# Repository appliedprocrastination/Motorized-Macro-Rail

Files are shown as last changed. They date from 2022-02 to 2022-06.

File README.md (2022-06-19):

# OpenMacroRail Electronics Hardware
## Summary
PCB-design for controlling a motorized macro rail. Designed for photographers with electronics skills rather than engineers with photography skills. Main features:
- Zero surface mount components, and should therefore be possible to hand solder - even for people with novice soldering skills. 
- Flexible solution for connecting to most types of camera via 2.5mm stereo jack, pin header, or solder joints.
- Simple design for driving a single motor via a BTT TMC2209 V1.2 motor driver.
- Based on the WiFi-enabled NodeMCU 32S V2 DevKit. 
- Has broken out headers for connecting limit switches and rotary encoders (neither of which are used in the intended application the board was designed for).
- Total cost of around $30 (Camera, optics, motor, slider, and tools not included)

### Other parts of this project:
- [Firmware and web-interface](https://github.com/AppliedProcrastination/OpenMacroRail)
- [3D printable gears and PCB mount](https://www.printables.com/model/219042-motorized-camera-rail-for-macro-photography) 
- [3D printable microscope objective adapter](https://www.printables.com/model/218910-microscope-objective-adapter) (RMS Thread 160mm focal distance)
- [Canon EF/EF-S mount for the microscope adapter above](https://www.printables.com/model/218900-canon-efef-s-lens-mount-with-screw-holes)
- Section of README with links to other relevant documentation: [Various Documentation](#various-documentation)

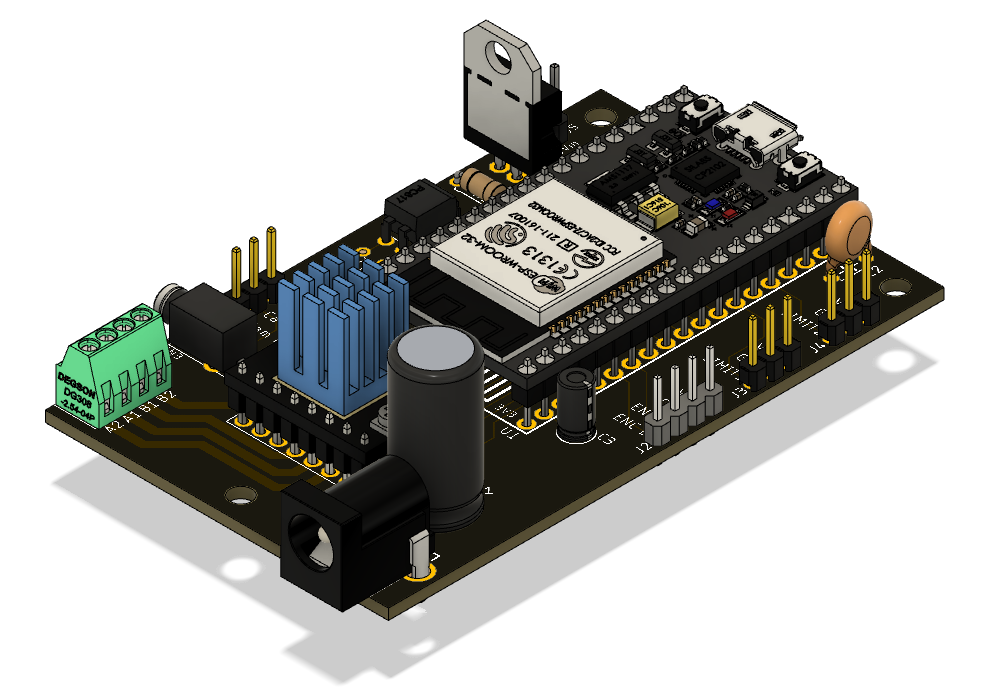
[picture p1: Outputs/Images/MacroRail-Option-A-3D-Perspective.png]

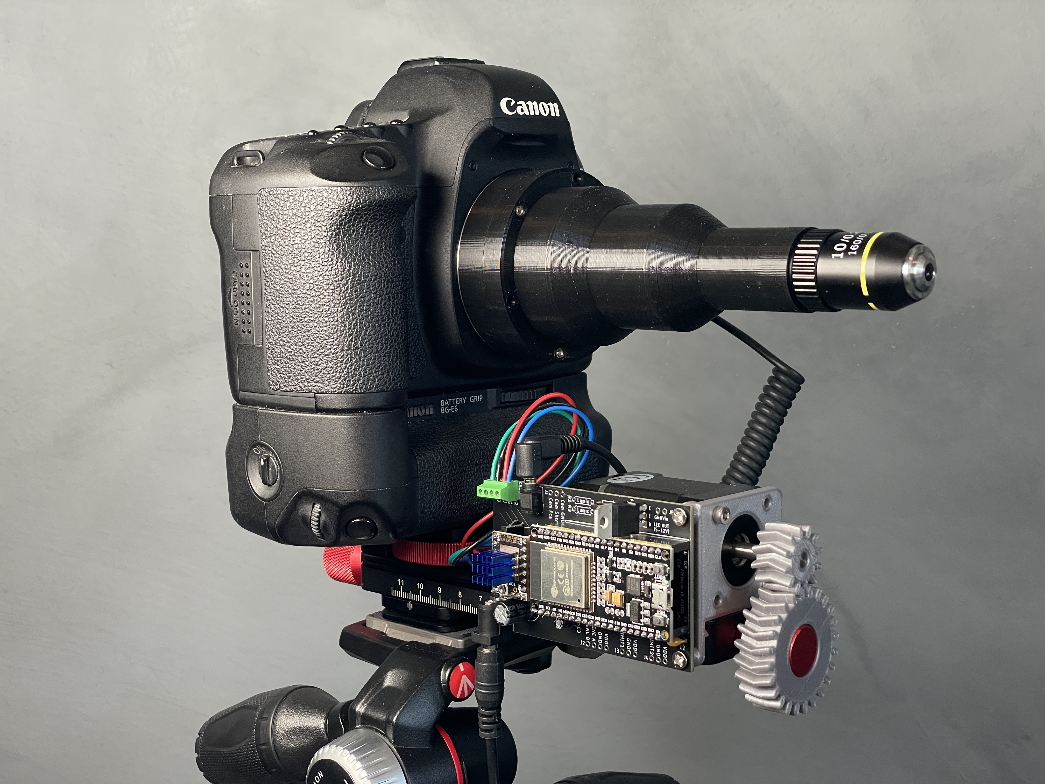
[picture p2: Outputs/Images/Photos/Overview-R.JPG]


## Configurability
The design is quite adaptable in general, and there are few components that are completely necessary for functioning (see the section "Minimum viable design"). There is however one part of the circuit that is particularly adaptable, and requires the users attention to guarantee a working configuration: the shutter control circuit - which depends on what kind of camera you are planning to control with this setup.

Snippet of schematic (DNP = Do Not Place):

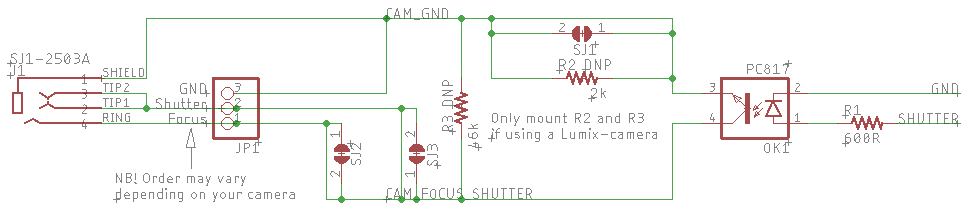
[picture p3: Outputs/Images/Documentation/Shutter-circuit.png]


As shown in the image above, there is a lot going on for what is normally a very simple circuit (you can trigger many cameras by simply short-circuiting all the pins in the remote shutter connector with a piece of wire). The reason for all this additional complexity is to keep the design as flexible as possible, and hopefully allow the PCB to be used with any type of camera. This is obviously not possible for me to test out in person, so I'm basing most of what follows on [this blog-post by Günter from LRTimelapse](https://lrtimelapse.com/news/intervalometer-hack/) (which is based on feedback from a solid photographer community) and private conversations with Stefan from [CNCKitchen](https://www.youtube.com/CNCKitchen) (as he owns a camera not mentioned in the above blog-post).

All the extra nick-nack is an attempt to solve the following design-requirements:
1. Different cameras require different signals to trigger
    - Example: 
        - Canon requires Shutter and GND to be shorted
        - Nikon/Sony requires Shutter, Focus and GND to be shorted
        - Lumix requires a [resistor network](https://i1.wp.com/fluxing.de/wp-content/uploads/2018/03/arduino-panasonic-lumix-shutter-schematic.jpg) between Shutter and GND.
2. Different cameras may swap the layout of Shutter and Focus signals on the 2.5mm jack
3. The user may not own a connector with a 2.5mm jack, so a pin header/2.54mm pitch solder joint option is also provided.
4. The high currents drawn by the motor may cause noise on the PCB, so therefore the shutter circuit is optically isolated from the rest of the electronics to avoid unintended triggering of the camera shutter.

The following components are layed out in the design solely to handle requirements 1. and 2.
- SJ1, SJ2, SJ3
- R2, R3 (Note: These are, to my knowledge, only required by Lumix - and should not be mounted by default)

The solder jumpers (SJ1-3) are there to give the user an opportunity to make permanent (but recoverable) changes to the circuit. The way this works is that each SJ consists of two exposed copper pads with a small trace connecting the pads. Cutting the trace with a scalpel will remove the connection between the pads, but it is still possible to recover this connection by applying a bit of solder as a bridge between the pads (in case the user buys a new camera, or just cut the wrong wire).

### An example of how to use solder jumpers:
Suppose your camera starts updating the screen each time the autofocus-signal is activated (even in manual focus mode), so you want to stop that signal from being activated each time a picture is captured. In this scenario, you can use a scalpel to break the wire connecting the two pads of SJ2 by cutting along the red arrow in the following picture: 

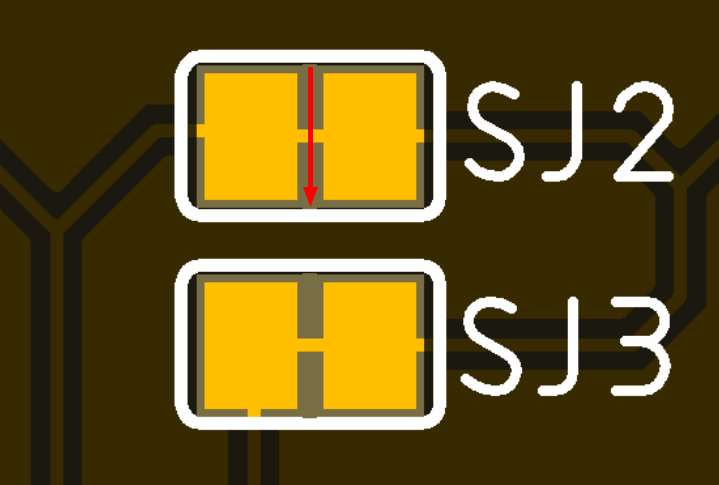
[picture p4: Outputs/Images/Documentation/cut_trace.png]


### Default configuration (Canon,Nikon,Sony):
The default configuration requires you to not mount R2 and R3. The pads on all the solder jumpers are shorted by default, meaning that a simplified schematic of the circuit looks like this:

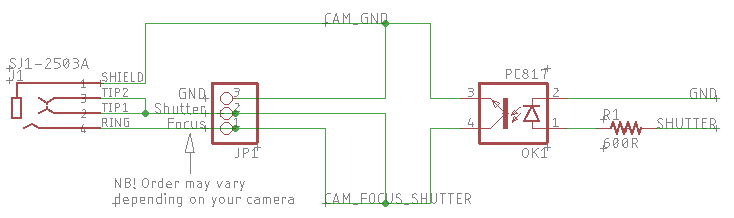
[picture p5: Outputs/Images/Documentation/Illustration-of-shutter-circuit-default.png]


This should work for most Canon, Nikon, and Sony cameras.

### Lumix configuration:
To use the shutter circuit with a Lumix camera, the resistor network must be mounted (R2 and R3). Keep in mind that SJ1 is shorted by default, meaning that it needs to be cut in order for R2 to take any effect.

Mount R2 and R3, then use a scalpel to break the wire in SJ1 by cutting along the red arrow in this picture.

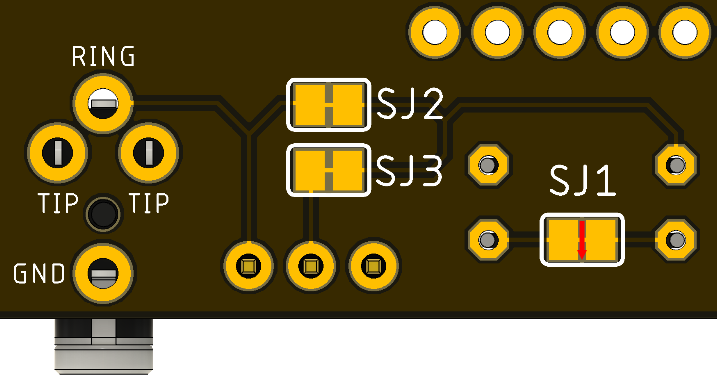
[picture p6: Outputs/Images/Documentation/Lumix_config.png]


Cutting this wire will activate R2 and leave you with the following schematic:

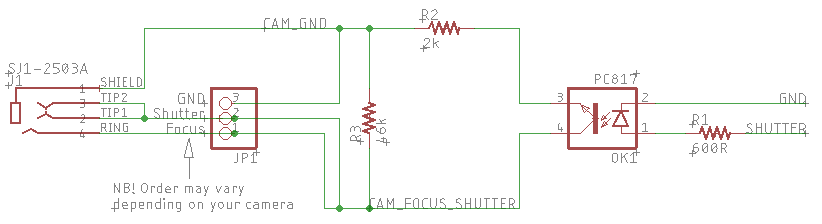
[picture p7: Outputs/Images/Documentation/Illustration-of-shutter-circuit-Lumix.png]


## Layout Options 
In the folder named Outputs/Gerber you will find design files that can be sent to a PCB manufacturer for production. There are two options, A and B, which differ only in the orientation of the power connector. 
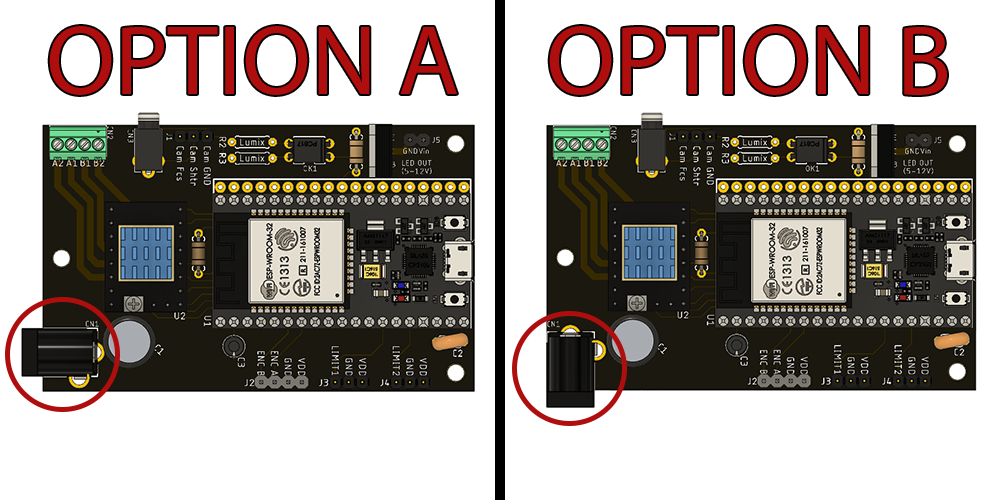
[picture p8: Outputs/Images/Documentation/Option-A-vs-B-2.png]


The reason that there are two options is to accommodate for mounting the PCB on different tripod designs. Keep in mind that the PCB is mounted on a moving part of the macro rail, so protruding parts may get stuck or bent by the force from the motor.
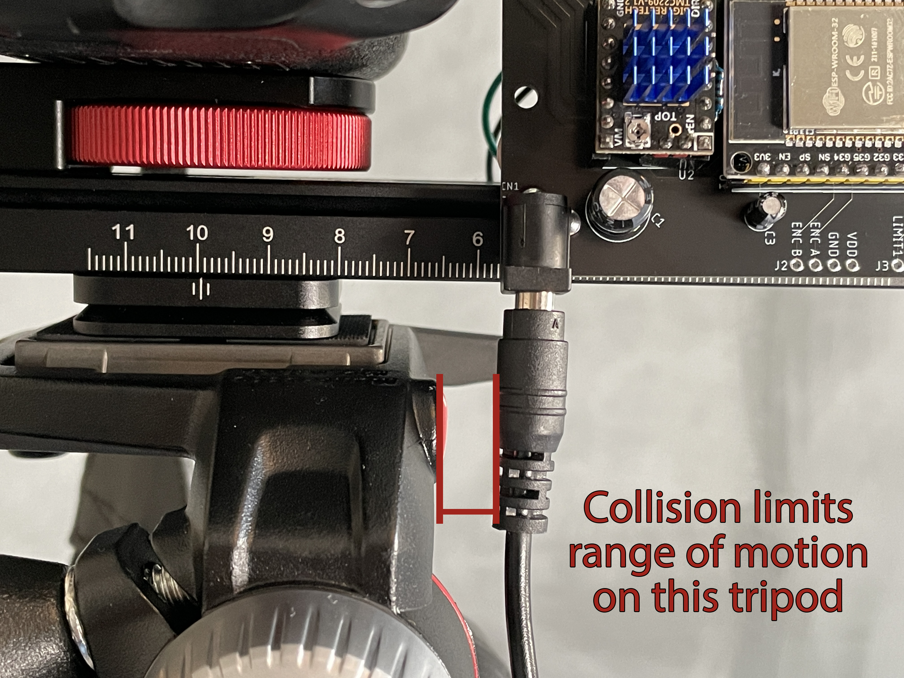
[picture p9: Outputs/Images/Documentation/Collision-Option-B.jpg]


## Bill Of Materials (BOM)
*Most of the AliExpress links are affiliate links. Prices are estimates and may vary with your location (shipping cost)*

### On PCB:
 - [PCB itself](./Outputs/Gerber/MacroRail_V1_0-2022-02-26.zip). Ca $10 at JLCPCB
 - 1x [TMC2209-V1.2](https://s.click.aliexpress.com/e/_9uc1XB) Stepper motor driver ([Documentation](https://github.com/bigtreetech/BIGTREETECH-TMC2209-V1.2/)). ca $8
 - 1x [NodeMCU 32s V2](https://www.aliexpress.com/item/1005001636295529.html) Dev kit (38-pin version) ([Documentation](https://docs.ai-thinker.com/en/esp32/boards/nodemcu_32s)) ca $5
 - 1x [PC817 Optocoupler](https://s.click.aliexpress.com/e/_AAgoAp) ca $1
 - 1x [100 uF capacitor (35V)](https://s.click.aliexpress.com/e/_ADnqKh) ca $1
 - 1x [10 uF capacitor (25V)](https://s.click.aliexpress.com/e/_ADnqKh) ca $1
 - 1x [1 uF capacitor](https://s.click.aliexpress.com/e/_9j2jOz) ca $1
 - 1x [2.1 mm Barrel Jack (power)](https://s.click.aliexpress.com/e/_Aq01NT) ca $1
 - 1x [Selection of resistors](https://s.click.aliexpress.com/e/_AOqGqt) (depending on your camera) ca $1
    - Note: R1 and R4 must always be mounted (these are 600 Ohm and 1k Ohm resistors respectively)
 - 1x [SJ1-2503A 2.5 mm stereo jack receptacle (for shutter cable)](https://no.mouser.com/ProductDetail/CUI-Devices/SJ1-2503A?qs=WyjlAZoYn52728cbIH3aBA%3D%3D) ca $1 (optional)
 - 1x [4-pin screw terminal block](https://s.click.aliexpress.com/e/_97dipR) ca $2 (optional)
 - 1x [TIP120 transistor (for powering external LED lighting)](https://s.click.aliexpress.com/e/_ApnAYv) ca $1 (optional) 
 - 3x [3-pin pin row](https://s.click.aliexpress.com/e/_ABvcat) ca $1 (optional)
 - 1x [4-pin pin row](https://s.click.aliexpress.com/e/_ABvcat) ca $1 (optional)
 - 1x [2-pin pin row](https://s.click.aliexpress.com/e/_ABvcat) ca $1 (optional)
 - 2x [19-pin pin header](https://s.click.aliexpress.com/e/_AFHrY5) ca $2 (optional)
 - 2x [8-pin pin header](https://s.click.aliexpress.com/e/_AFHrY5) ca $1 (optional)
 - 1x [2-pin pin header](https://s.click.aliexpress.com/e/_AFHrY5) ca $1 (optional)

 Total on PCB: ca $40 ($29 when excluding optional components)

### Outside of PCB:
Mandatory parts:
 - [Macro Rail](https://s.click.aliexpress.com/e/_9IiOvB) ca. $20 
 - [Nema 14 high torque motor](https://s.click.aliexpress.com/e/_ArX3ot) (High torque may be unnecessary for moving compact cameras) ca $20
 - RMS threaded microscope lens (focused to 160mm). [Example](https://s.click.aliexpress.com/e/_9zATGv) ca $8
 - 5-12V Power supply (current can be limited with TMC2209 if 5V is too much for your motor). [Example](https://s.click.aliexpress.com/e/_AC81D7) ca $8 
 - Cable for shutter release that fits your camera (you can either use the 2.5mm jack receptacle or cut the cable and solder it directly to the PCB via JP1)
    - [Example for various cameras](https://s.click.aliexpress.com/e/_9iNl7J) ca $3

Parts that can be 3D-printed if you design something that suits your camera:
 - Bellow spacer that fits your camera (with converters to hold the microscope lens). This is optional, and can be 3D printed instead. 
    - Examples for Canon 5D:
        - [Bellow spacer](https://s.click.aliexpress.com/e/_A5xnYt) ca $40
        - [EFS to M24 converter](https://s.click.aliexpress.com/e/_9QvErF) ca $5
        - [M42 to RMS converter](https://s.click.aliexpress.com/e/_9QPTOd) ca $5
 
Total outside of PCB: ca $109 ($59 when excluding parts that can be 3D-printed)

## Preview

### Top

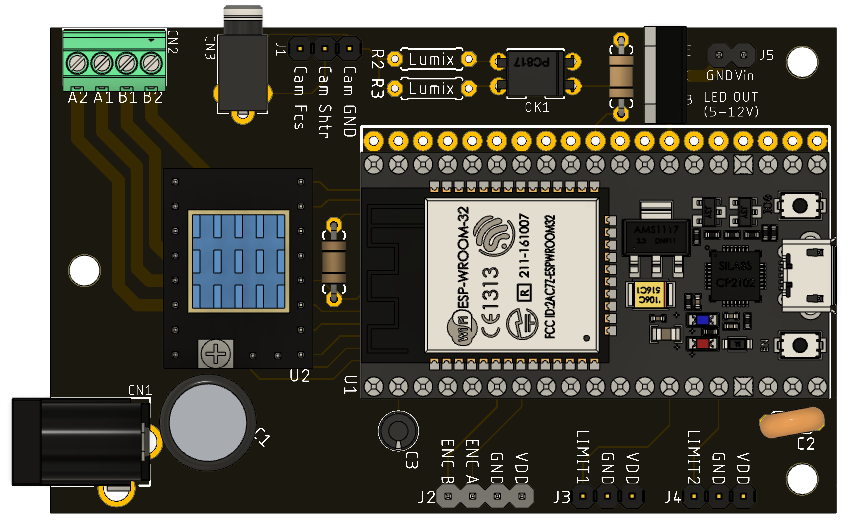
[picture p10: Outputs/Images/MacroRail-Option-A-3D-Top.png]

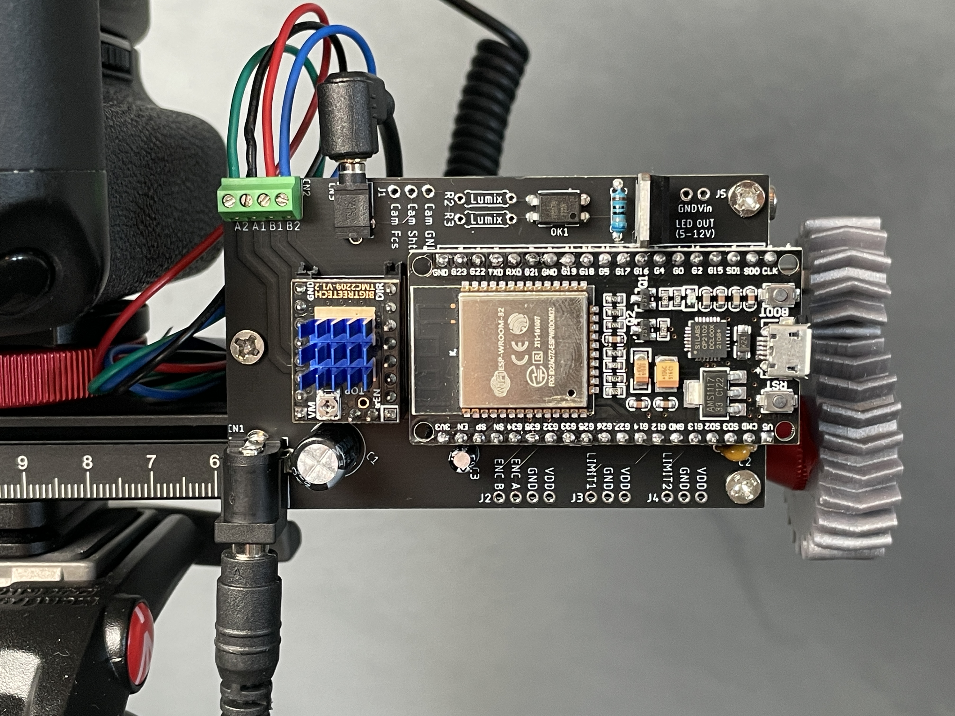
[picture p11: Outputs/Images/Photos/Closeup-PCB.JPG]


### Bottom

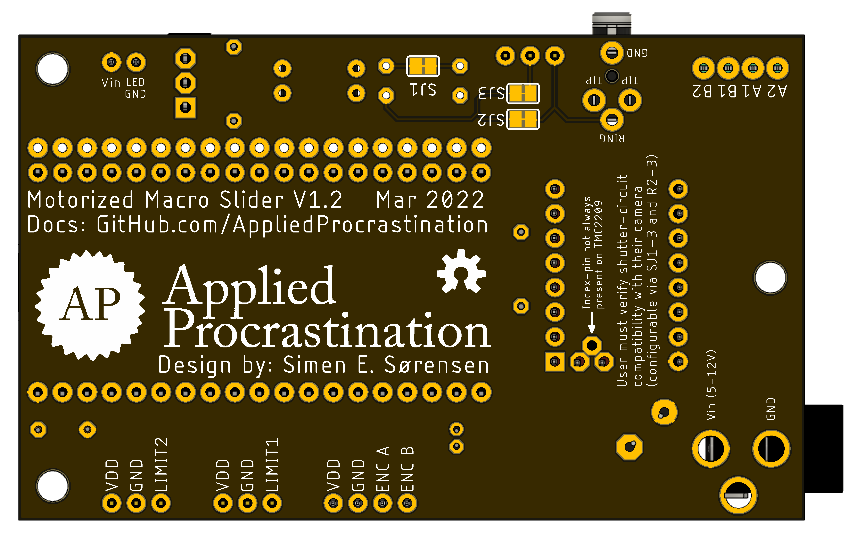
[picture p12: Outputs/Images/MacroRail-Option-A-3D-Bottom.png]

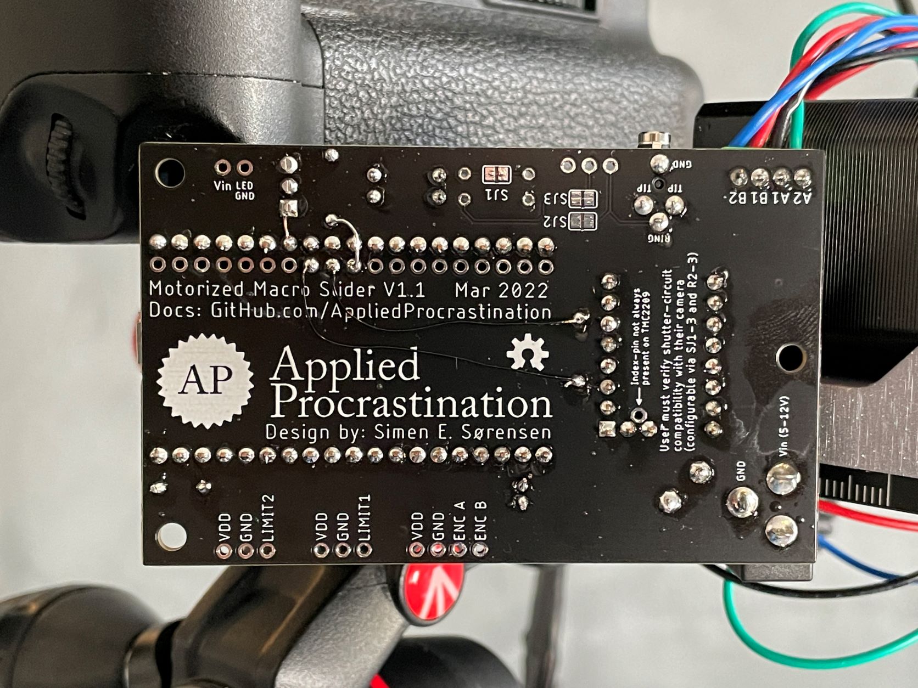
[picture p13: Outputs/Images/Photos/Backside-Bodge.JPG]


### Minimum viable design
Note: You may need to mount more resistors to get a minimum viable design (depending on your camera)

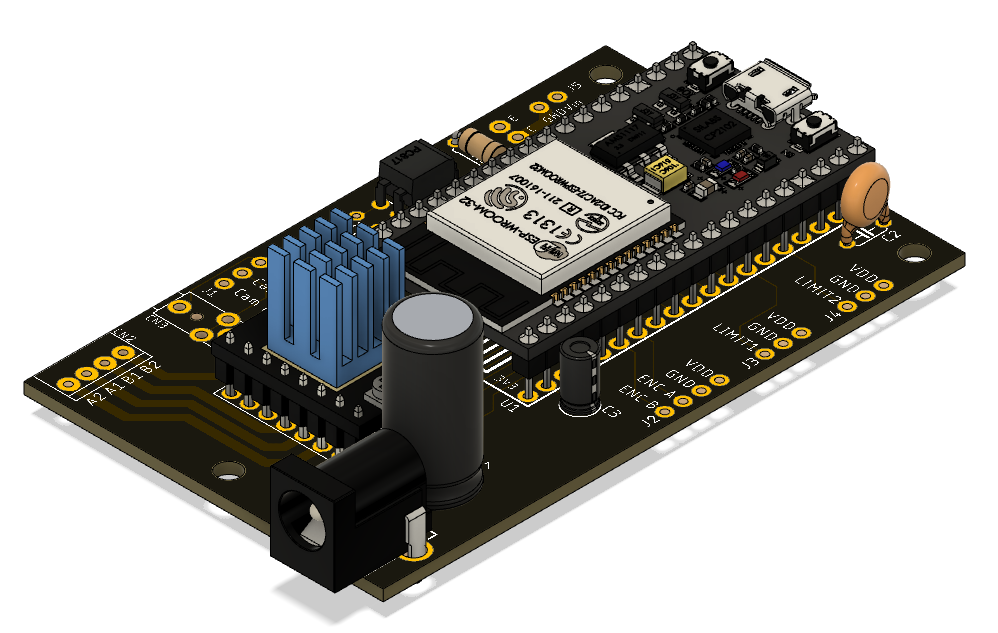
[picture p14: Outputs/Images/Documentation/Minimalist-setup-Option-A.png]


## How to order a printed circuit board (PCB)?
If you are interested in this project, and feel comfortable soldering electronic components, but have never ordered a custom PCB before this section is for you. 

Hobby-grade PCB manufacturers have made the process of ordering custom PCBs incredibly simple (and cheap) over the last few years, so for a low complexity board like this one, ordering can be done without any prior knowledge of the manufacturing process. 

### Step by step guide:

1. Decide whether you want your power connector oriented sideways (Option A) or downwards (Option B). Try to think about whether the power cable may get in the way of movement the tripod you plan to mount your macro rail to. See the section about [Layout Options](#layout-options) for more info.
2. Download the .zip file corresponding to your preferred layout option from the folder [/Outputs/Gerber](/Outputs/Gerber/). This is the design file that you will send to the manufacturer for fabrication.
3. Go to your preferred PCB manufacturers website and upload the gerber file. This board was designed for using https://www.jlcpcb.com, which is a very cheap, and fast, hobby-grade manufacturer. 

4. Once the upload is complete, you will see a preview of the board, and the web-tool will have learned most of the important parameters of the design (like the size, how many layers of copper it contains, etc.)
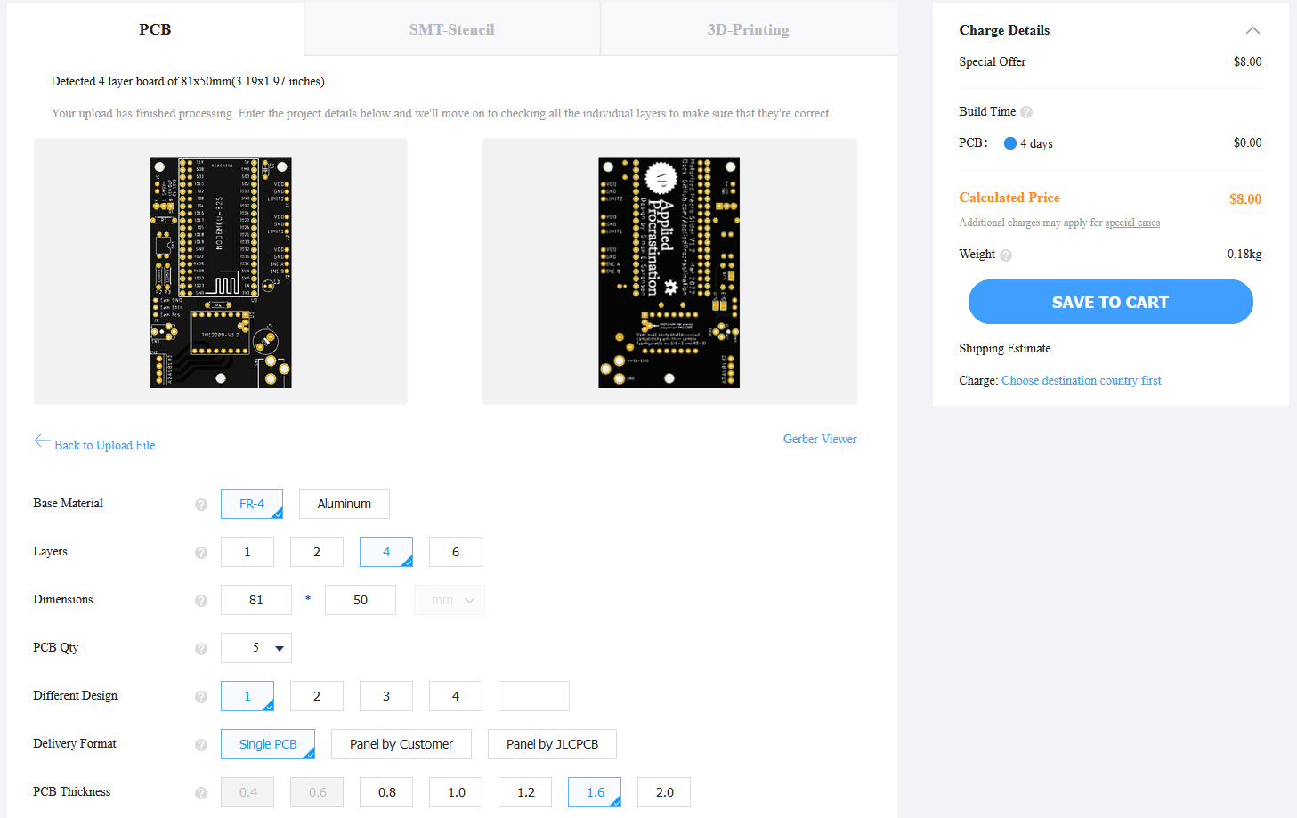
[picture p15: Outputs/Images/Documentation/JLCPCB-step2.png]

5. There's only one important thing you may need to fill in, which is the order of the layers. For some reason, the web-tool doesn't recognize the _l1, _l2, _l3, and _l4, suffixes of each layer, so you need to select these layers as shown in the image below. 
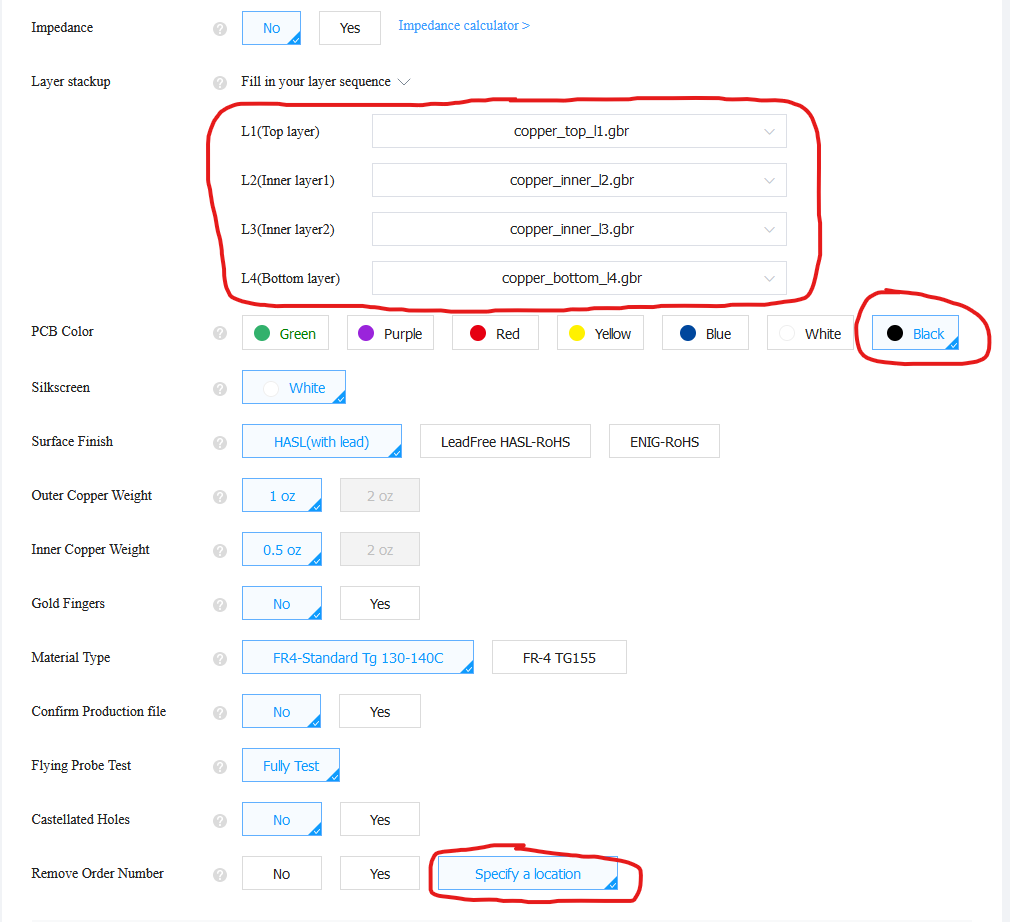
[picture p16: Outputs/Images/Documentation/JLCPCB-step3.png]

While you are at it, make sure to select the sexy black soldermask, and click "specify a location" for the order number. The last setting will ensure that the manufacturer doesn't place an order number anywhere important, but rather replace a predefined string like shown here:
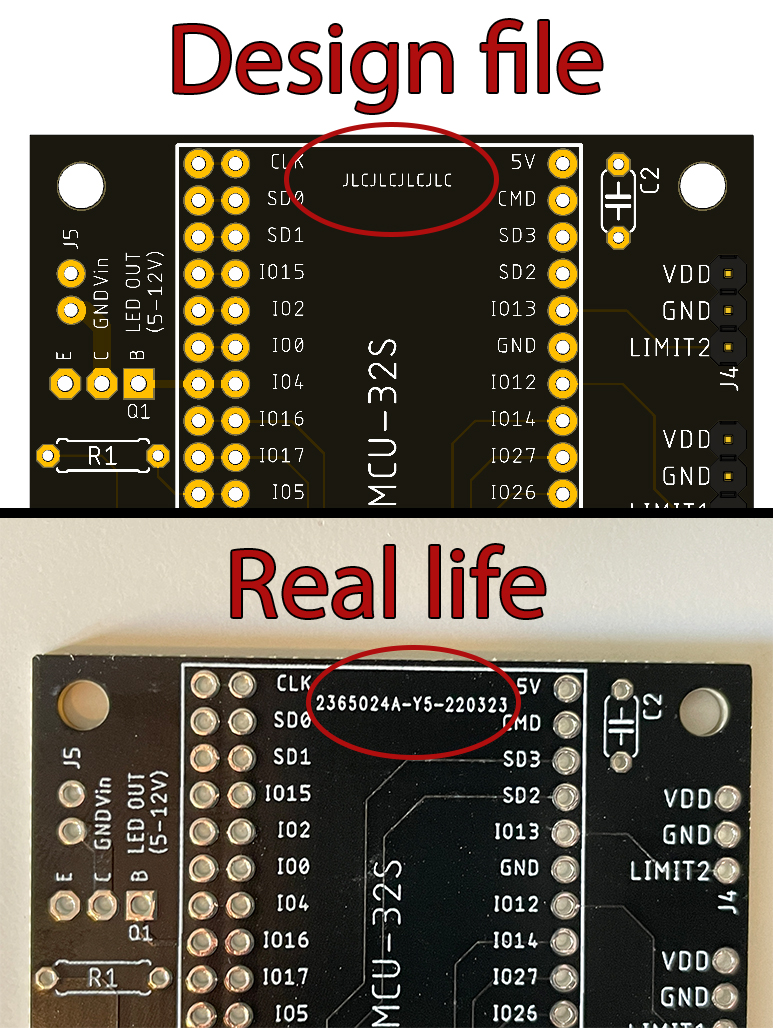
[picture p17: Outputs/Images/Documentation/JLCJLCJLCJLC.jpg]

6. That's it! Click "Save to cart", pay, and the board will be manufactured and shipped towards you within a two or three days (typically). Note that there is a cheap shipping option kind of hidden in the menu. If you didn't already have all the other necessary components in your electronics stockpile, it might be a good idea to consider this "slow" shipping option since you are already waiting for other stuff. In my experience, the PCBs arrive between 2 and 3 weeks after placing your order (when using the cheapest shipping option).
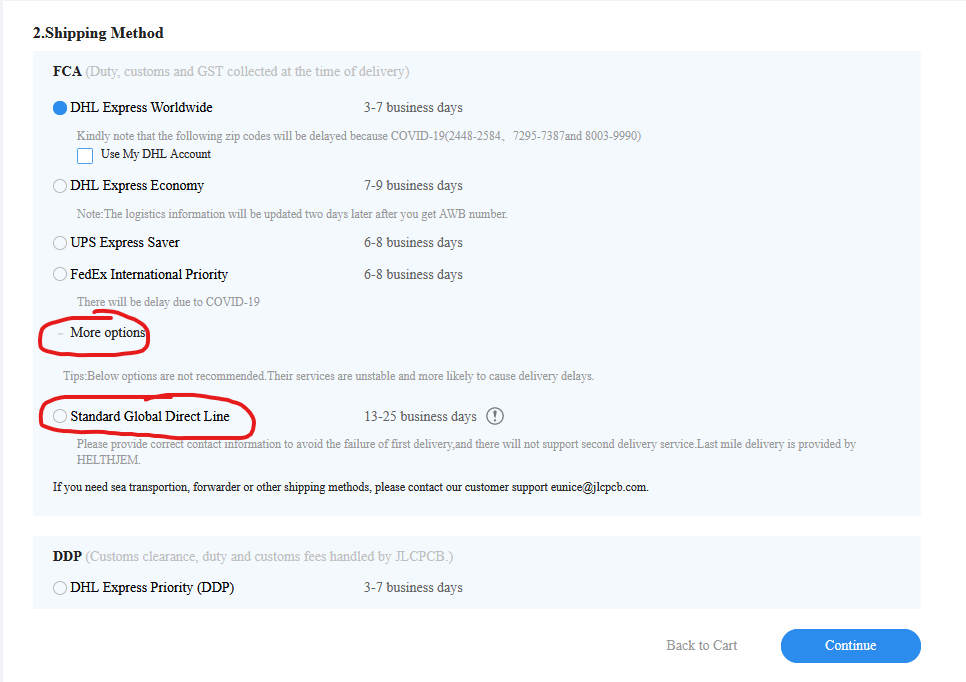
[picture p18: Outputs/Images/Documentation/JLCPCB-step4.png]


## Various documentation:
- [NodeMCU-32S Core Development Board](https://docs.ai-thinker.com/en/esp32/boards/nodemcu_32s)
- [NodeMCU Arduino Core (Software)](https://github.com/espressif/arduino-esp32)
- [TMC2209-V1.2 manual (Motor driver module)](https://github.com/bigtreetech/BIGTREETECH-TMC2209-V1.2/blob/master/manual/TMC2209-V1.2-manual.pdf)
- [TMC2209 datasheet (chip itself)](https://www.trinamic.com/fileadmin/assets/Products/ICs_Documents/TMC2209_datasheet_rev1.07.pdf)

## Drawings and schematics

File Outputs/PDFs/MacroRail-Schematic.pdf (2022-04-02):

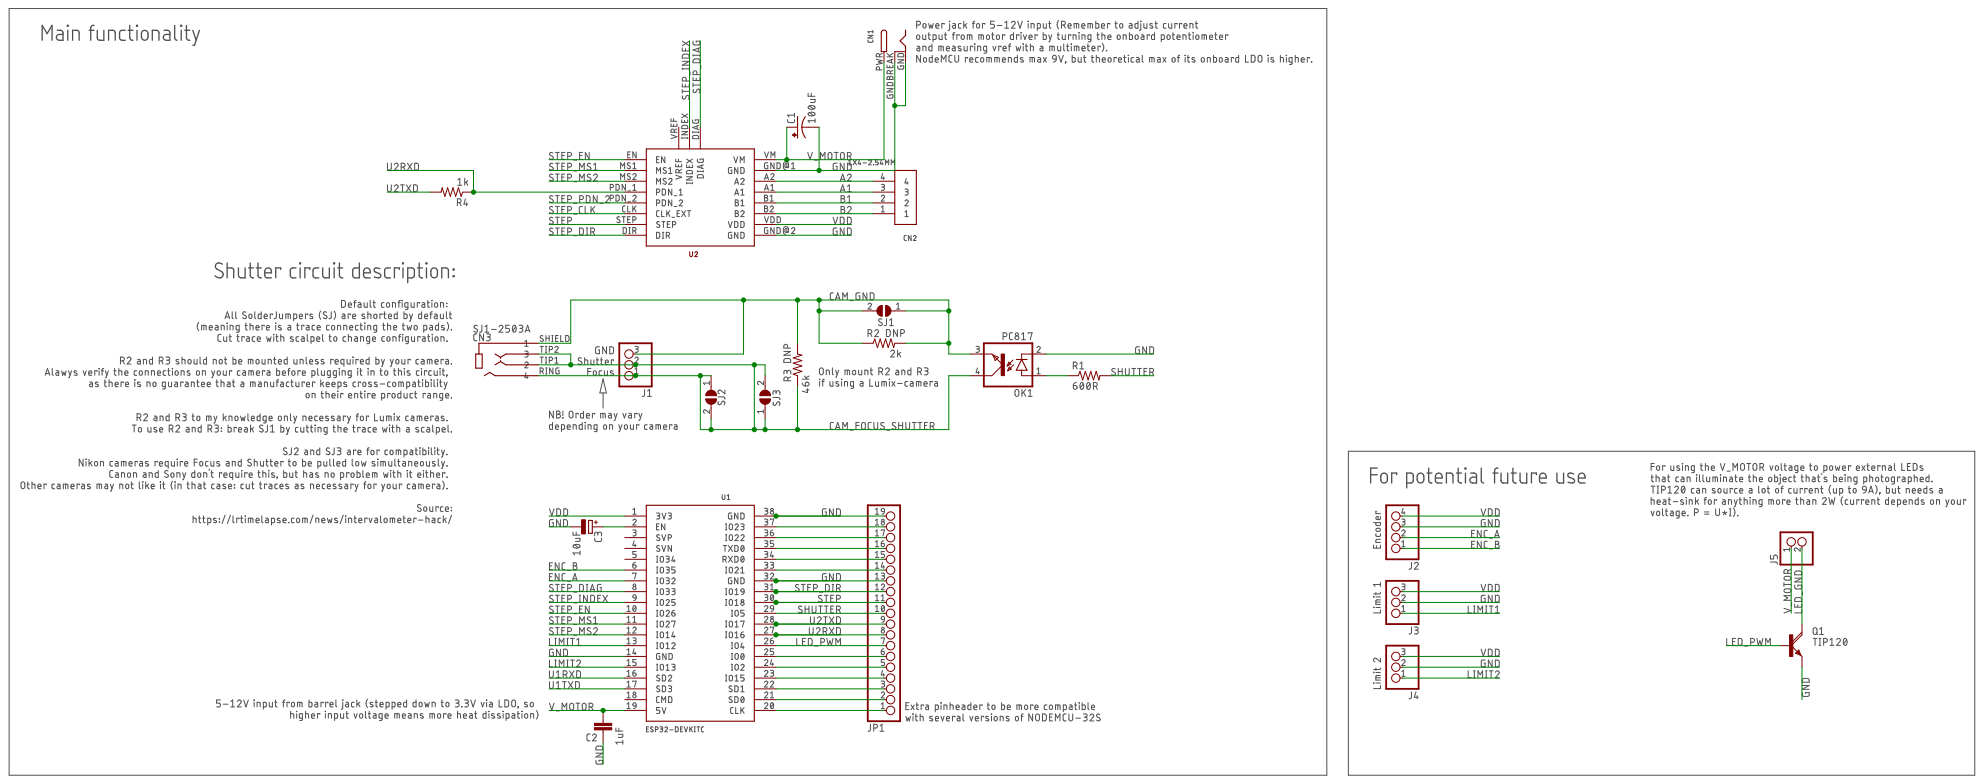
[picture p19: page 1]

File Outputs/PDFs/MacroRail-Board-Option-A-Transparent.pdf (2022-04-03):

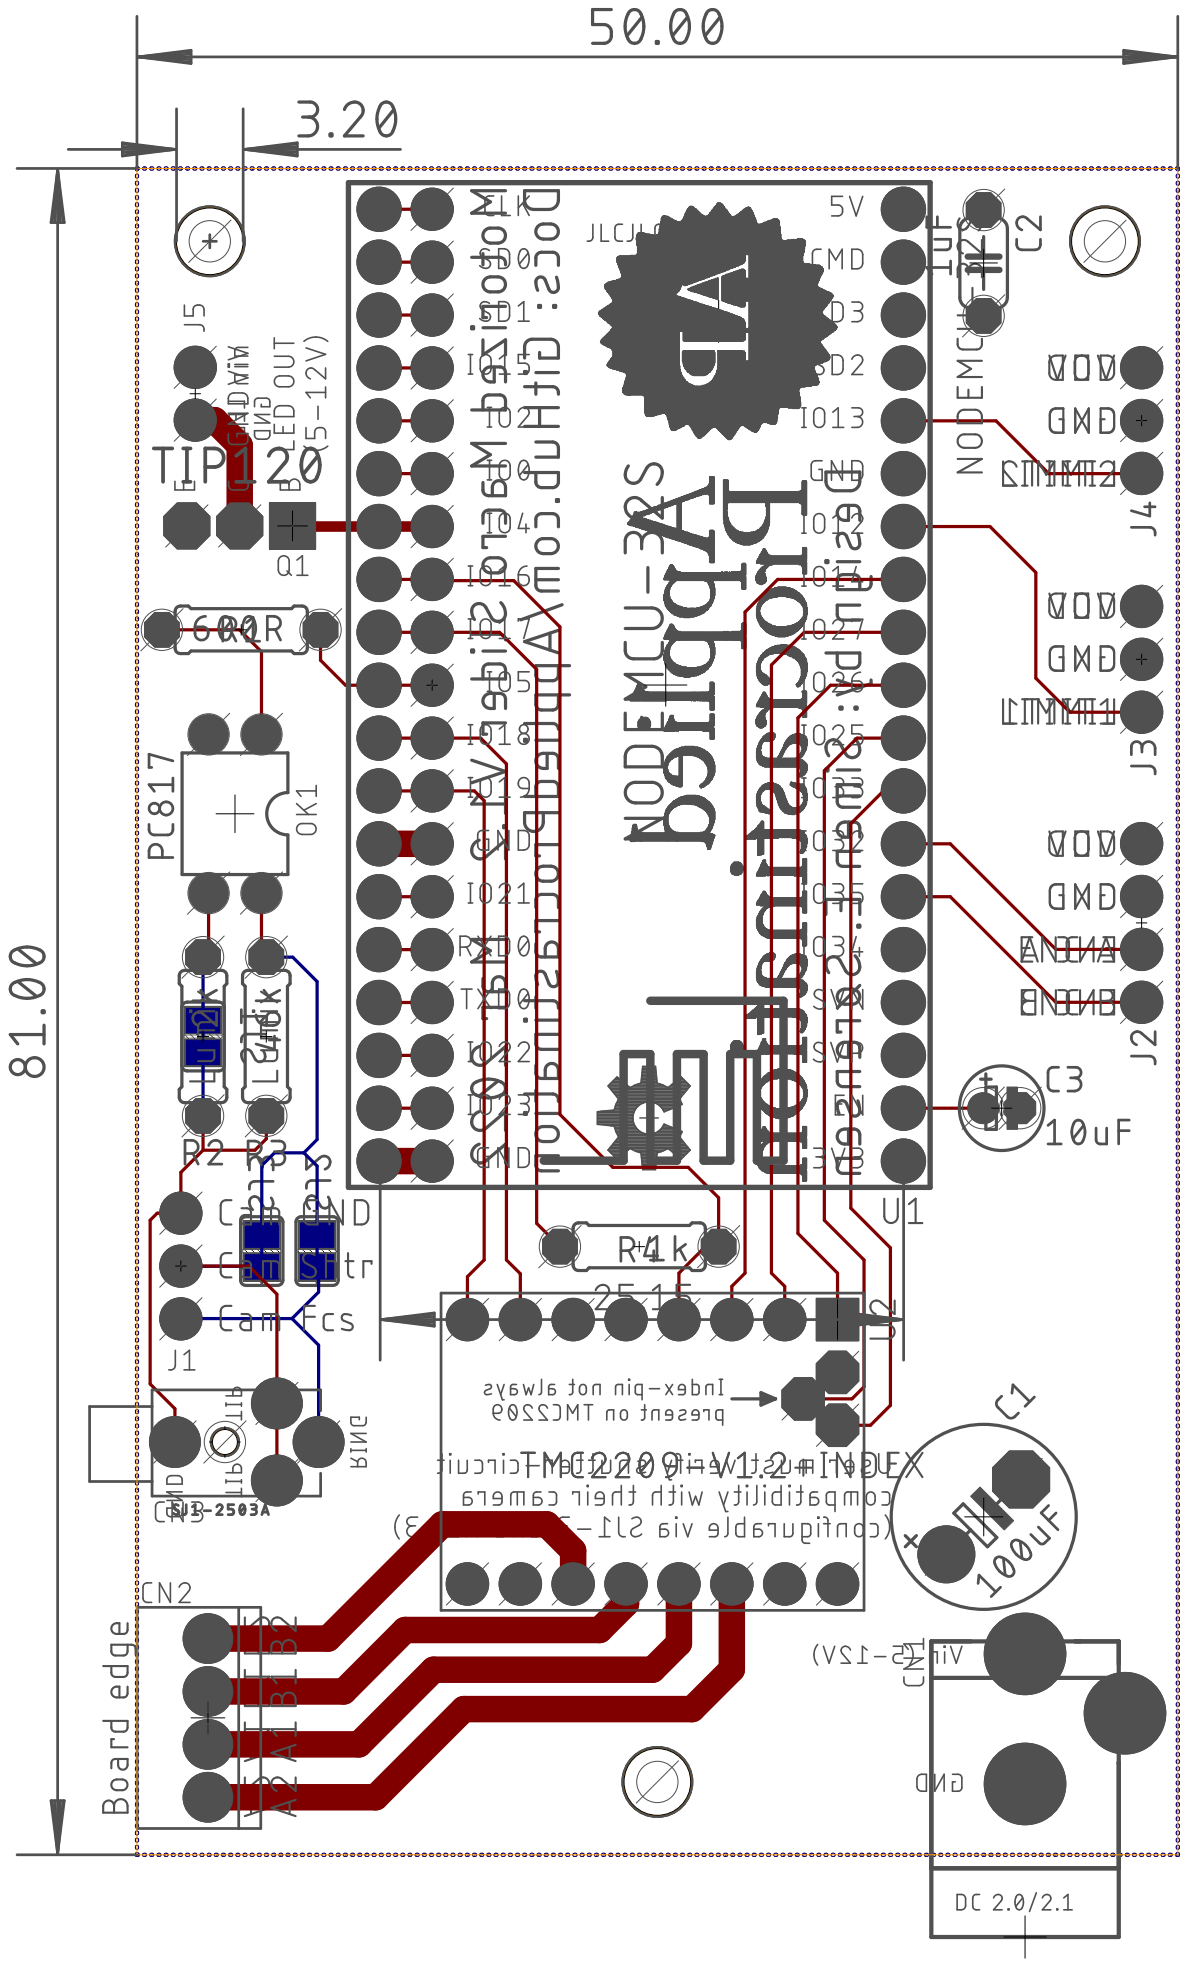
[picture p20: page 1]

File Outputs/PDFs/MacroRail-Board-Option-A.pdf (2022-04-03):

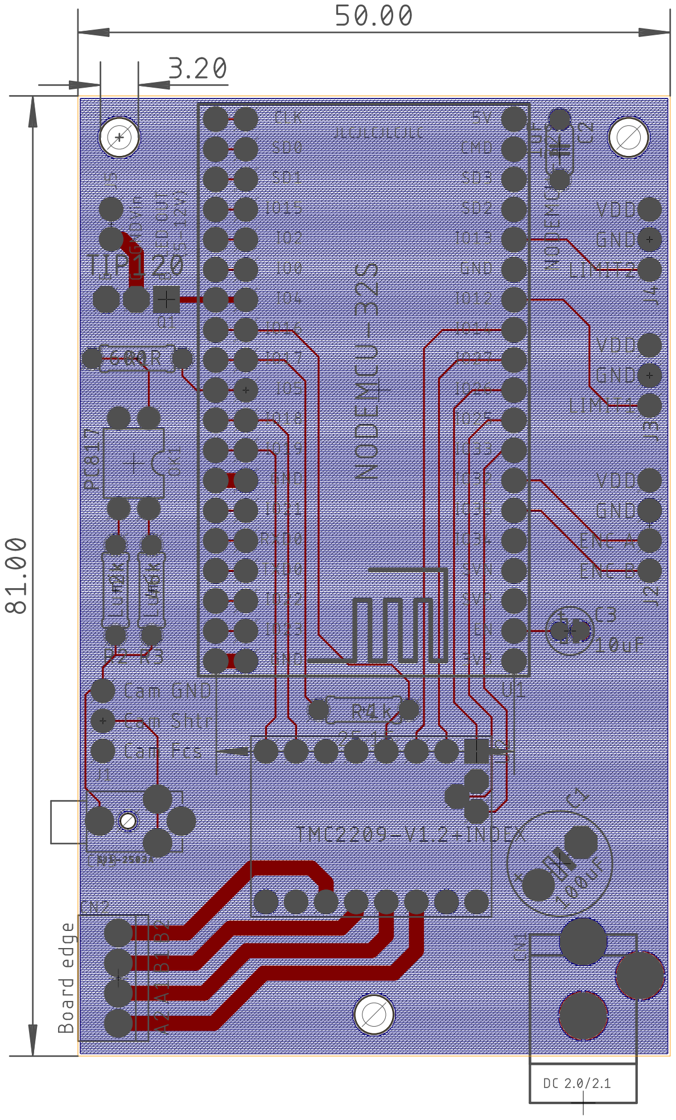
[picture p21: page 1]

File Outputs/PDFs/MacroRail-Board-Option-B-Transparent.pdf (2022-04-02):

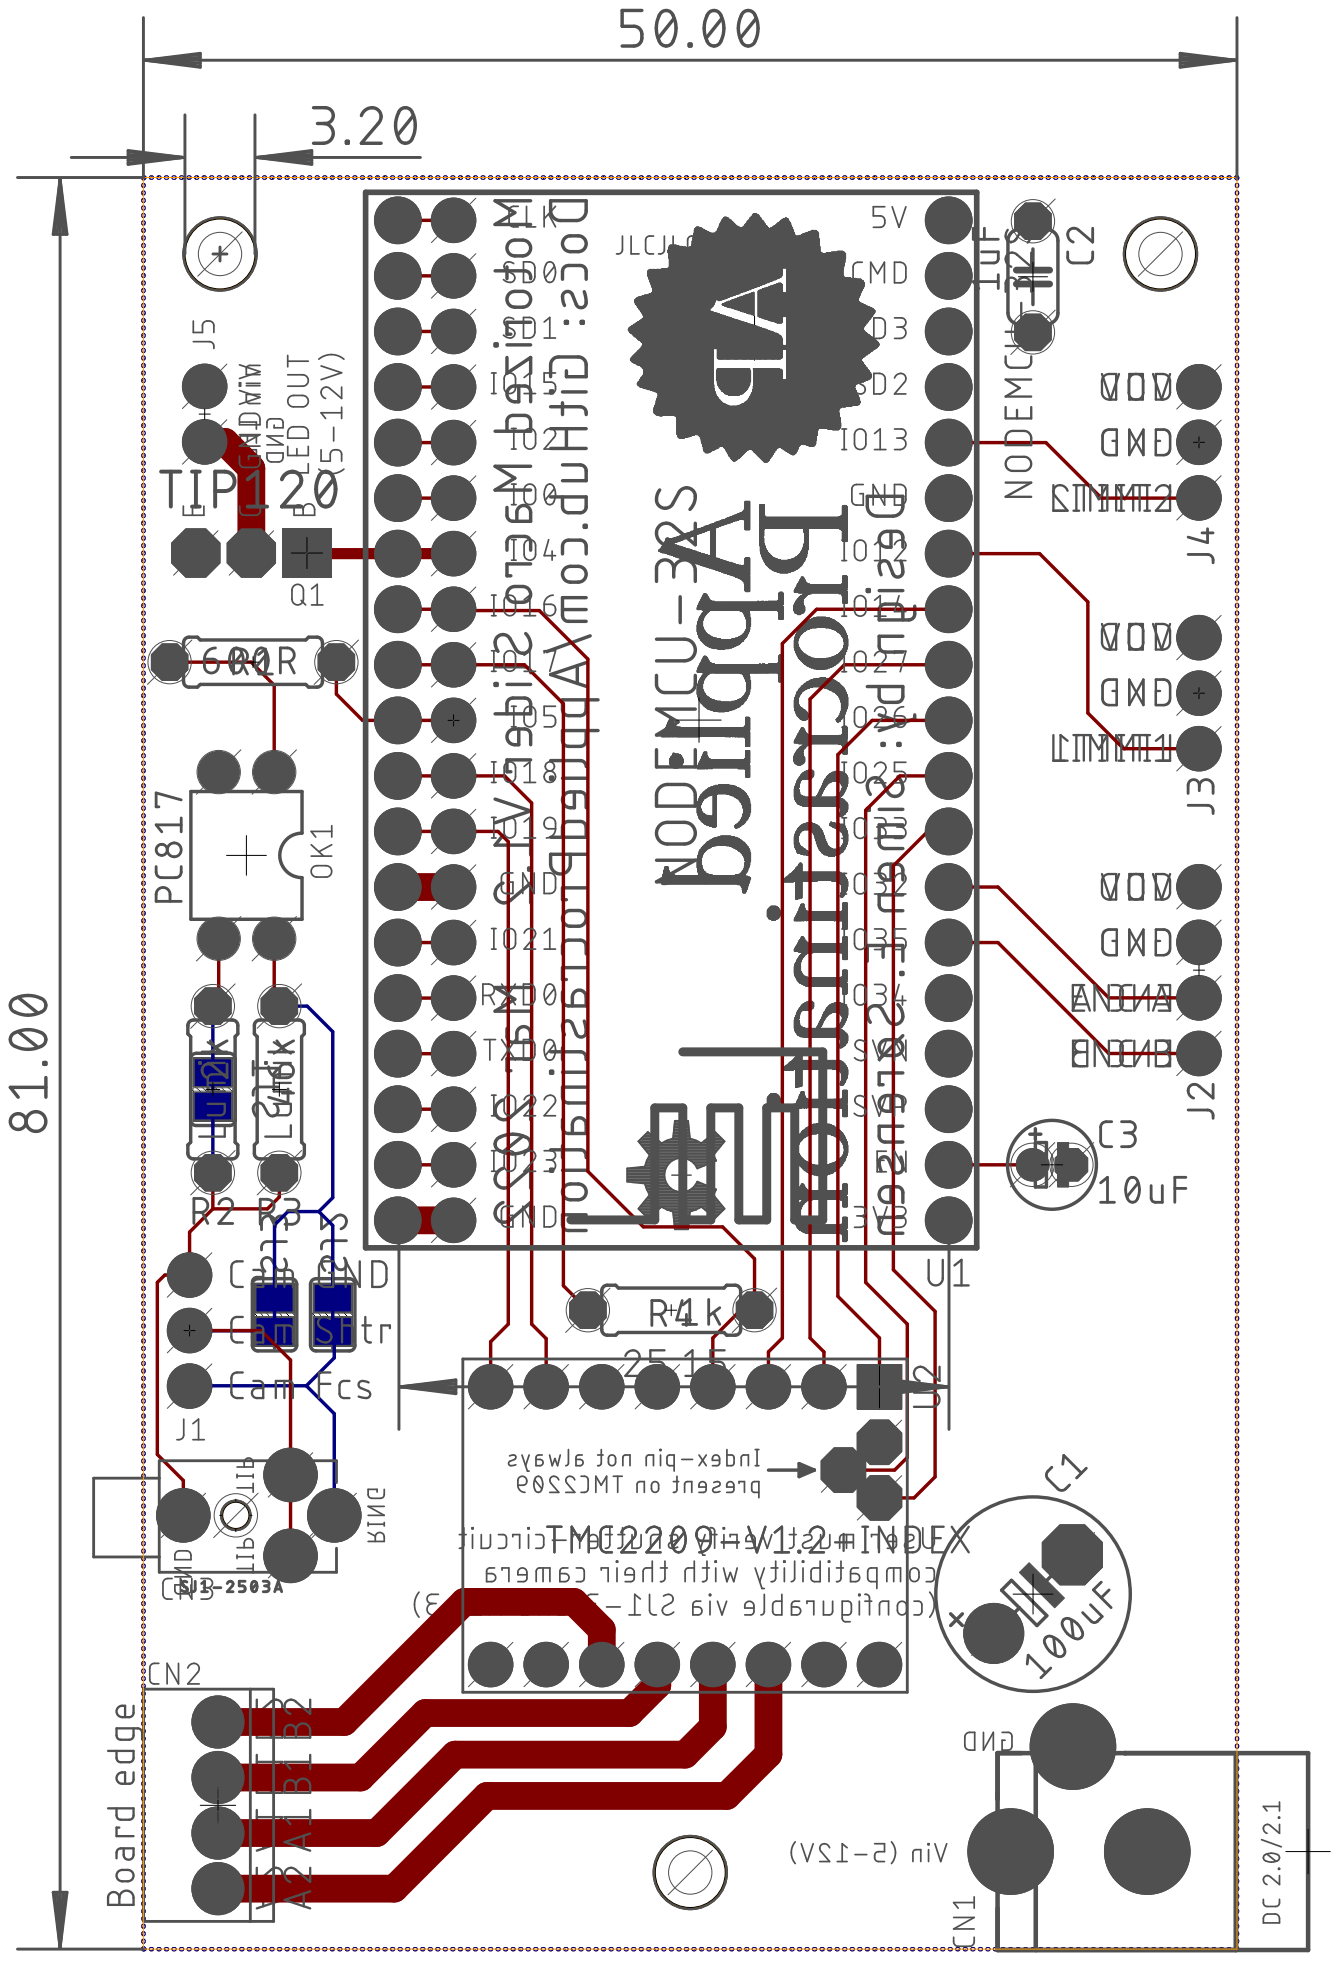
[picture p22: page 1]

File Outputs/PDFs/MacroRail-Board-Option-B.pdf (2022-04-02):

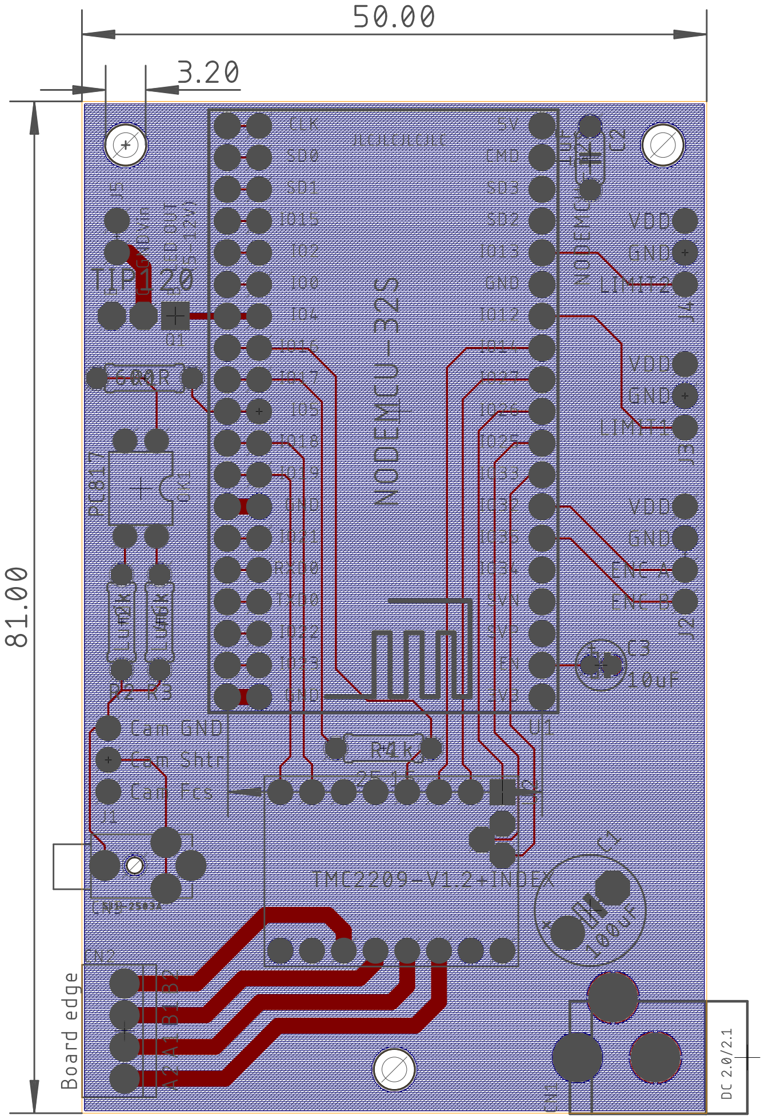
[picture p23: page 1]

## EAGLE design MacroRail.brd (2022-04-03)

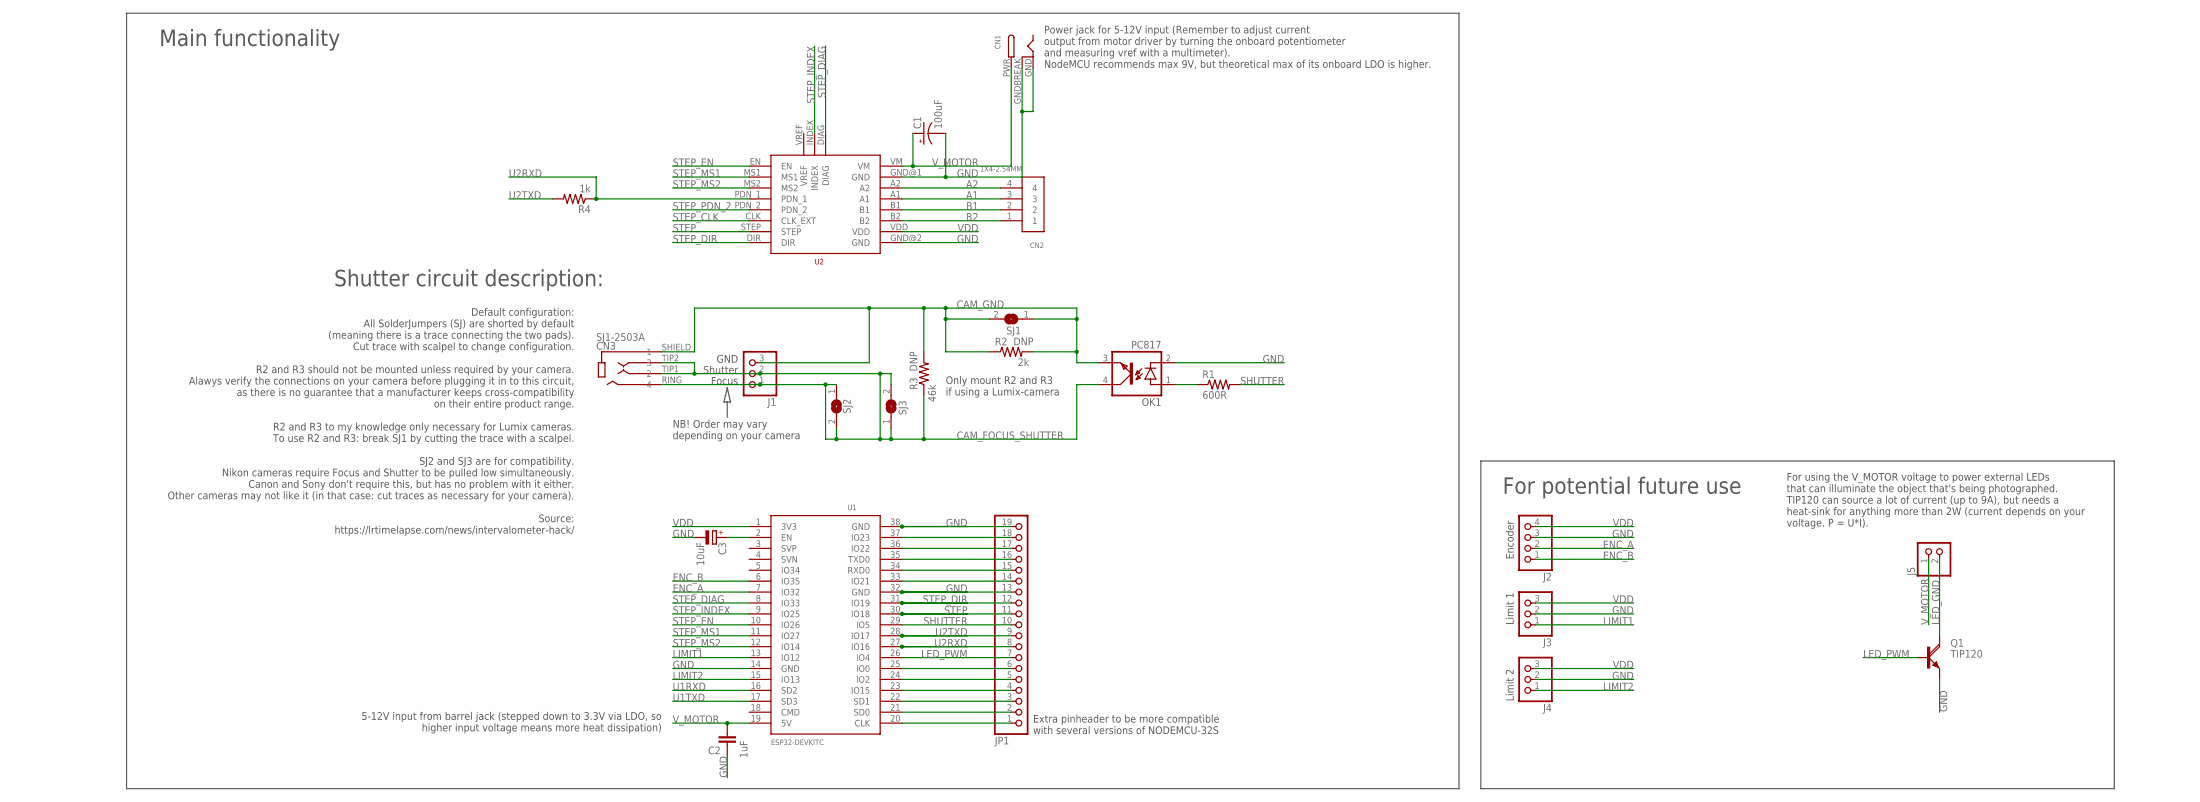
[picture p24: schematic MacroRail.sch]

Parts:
C1: 100uF; E5-8,5
C2: 1uF; C050-024X044
C3: 10uF; E1,8-4
CN1: DCBARRELPTH; DCJACK_2MM_PTH
CN2: 1X4-2.54MM; 1X04-2.54MM
CN3: SJ1-2503A; STEREOJACK2.5MM_STEREOJACK2.5MM
J1, J3, J4: PINHD-1X3CB; 1X03-CLEANBIG
J2: PINHD-1X4; 1X04
J5: PINHD-1X2CLEAN; 1X02CLEAN
JP1: PINHD-1X19; 1X19
OK1: PC817; DIL04
Q1: TIP120; TO220AH
R1: 600R; 0207/7
R2: 2k; 0207/7
R3: 46k; 0207/7
R4: 1k; 0207/7
SJ1, SJ2, SJ3: SJ
U1: ESP32DEVKITCWIDE; NODEMCU-32S
U2: TMC2209-V1.2+INDEX; BIGTREETECH-TMC2209-V1.2+INDEX

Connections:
A1: CN2.3, U2.A1
A2: CN2.4, U2.A2
B1: CN2.2, U2.B1
B2: CN2.1, U2.B2
CAM_FOCUS_SHUTTER: CN3.RING (4), CN3.TIP1 (2), CN3.TIP2 (3), J1.1, J1.2, OK1.4 (COL), R3.1, SJ2.1, SJ2.2, SJ3.1, SJ3.2
CAM_GND: CN3.SHIELD (1), J1.3, OK1.3 (EMIT), R2.1, R2.2, R3.2, SJ1.1, SJ1.2
ENC_A: J2.2, U1.7 (IO32)
ENC_B: J2.1, U1.6 (IO35)
GND: C1.-, C2.1, C3.-, CN1.GND, CN1.GNDBREAK, J2.3, J3.2, J4.2, JP1.13, JP1.19, OK1.2 (C), Q1.E, U1.14 (GND), U1.32 (GND), U1.38 (GND), U2.GND@1 (GND), U2.GND@2 (GND)
LED_GND: J5.2, Q1.C
LED_PWM: JP1.7, Q1.B, U1.26 (IO4)
LIMIT1: J3.1, U1.13 (IO12)
LIMIT2: J4.1, U1.15 (IO13)
unnamed: OK1.1 (A), R1.1
unnamed: C3.+, U1.2 (EN)
unnamed: JP1.18, U1.37 (IO23)
unnamed: JP1.17, U1.36 (IO22)
unnamed: JP1.16, U1.35 (TXD0)
unnamed: JP1.15, U1.34 (RXD0)
unnamed: JP1.14, U1.33 (IO21)
unnamed: JP1.6, U1.25 (IO0)
unnamed: JP1.5, U1.24 (IO2)
unnamed: JP1.4, U1.23 (IO15)
unnamed: JP1.3, U1.22 (SD1)
unnamed: JP1.2, U1.21 (SD0)
unnamed: JP1.1, U1.20 (CLK)
SHUTTER: JP1.10, R1.2, U1.29 (IO5)
STEP: JP1.11, U1.30 (IO18), U2.STEP
STEP_CLK: U2.CLK (CLK_EXT)
STEP_DIAG: U1.8 (IO33), U2.DIAG
STEP_DIR: JP1.12, U1.31 (IO19), U2.DIR
STEP_EN: U1.10 (IO26), U2.EN
STEP_INDEX: U1.9 (IO25), U2.INDEX
STEP_MS1: U1.11 (IO27), U2.MS1
STEP_MS2: U1.12 (IO14), U2.MS2
STEP_PDN_2: U2.PDN_2
U1RXD: U1.16 (SD2)
U1TXD: U1.17 (SD3)
U2RXD: JP1.8, R4.1, U1.27 (IO16), U2.PDN_1
U2TXD: JP1.9, R4.2, U1.28 (IO17)
VDD: J2.4, J3.3, J4.3, U1.1 (3V3), U2.VDD
V_MOTOR: C1.+, C2.2, CN1.PWR, J5.1, U1.19 (5V), U2.VM

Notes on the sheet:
GND
Focus
Shutter
Power jack for 5-12V input (Remember to adjust current output from motor driver by turning the onboard potentiometer and measuring vref with a multimeter). NodeMCU recommends max 9V, but theoretical max of its onboard LDO is higher.
5-12V input from barrel jack (stepped down to 3.3V via LDO, so higher input voltage means more heat dissipation)
Limit 1
Limit 2
Encoder
For potential future use
Main functionality
Default configuration: All SolderJumpers (SJ) are shorted by default (meaning there is a trace connecting the two pads). Cut trace with scalpel to change configuration. R2 and R3 should not be mounted unless required by your camera. Alawys verify the connections on your camera before plugging it in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
Shutter circuit description:
NB! Order may vary depending on your camera
Only mount R2 and R3 if using a Lumix-camera
For using the V_MOTOR voltage to power external LEDs that can illuminate the object that's being photographed. TIP120 can source a lot of current (up to 9A), but needs a heat-sink for anything more than 2W (current depends on your voltage. P = U*I).
Extra pinheader to be more compatible with several versions of NODEMCU-32S

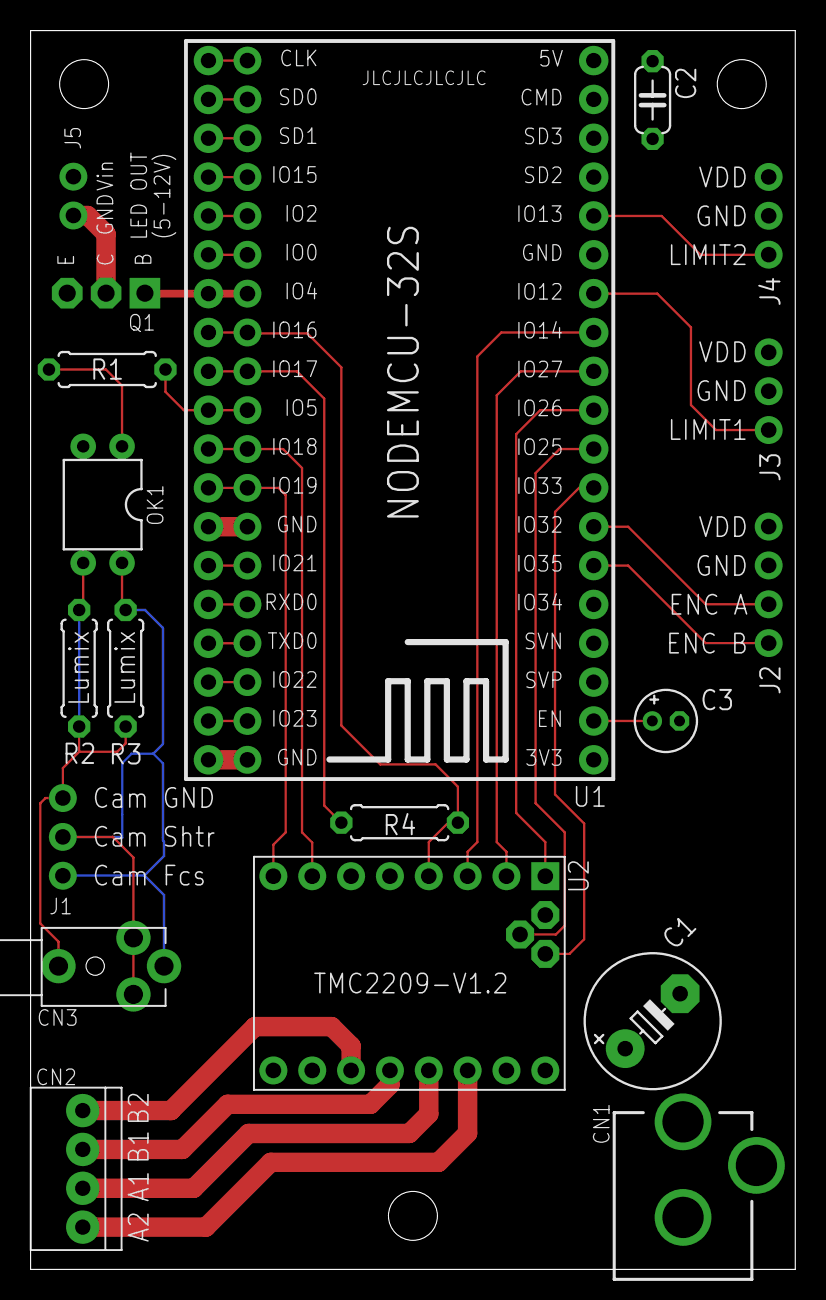
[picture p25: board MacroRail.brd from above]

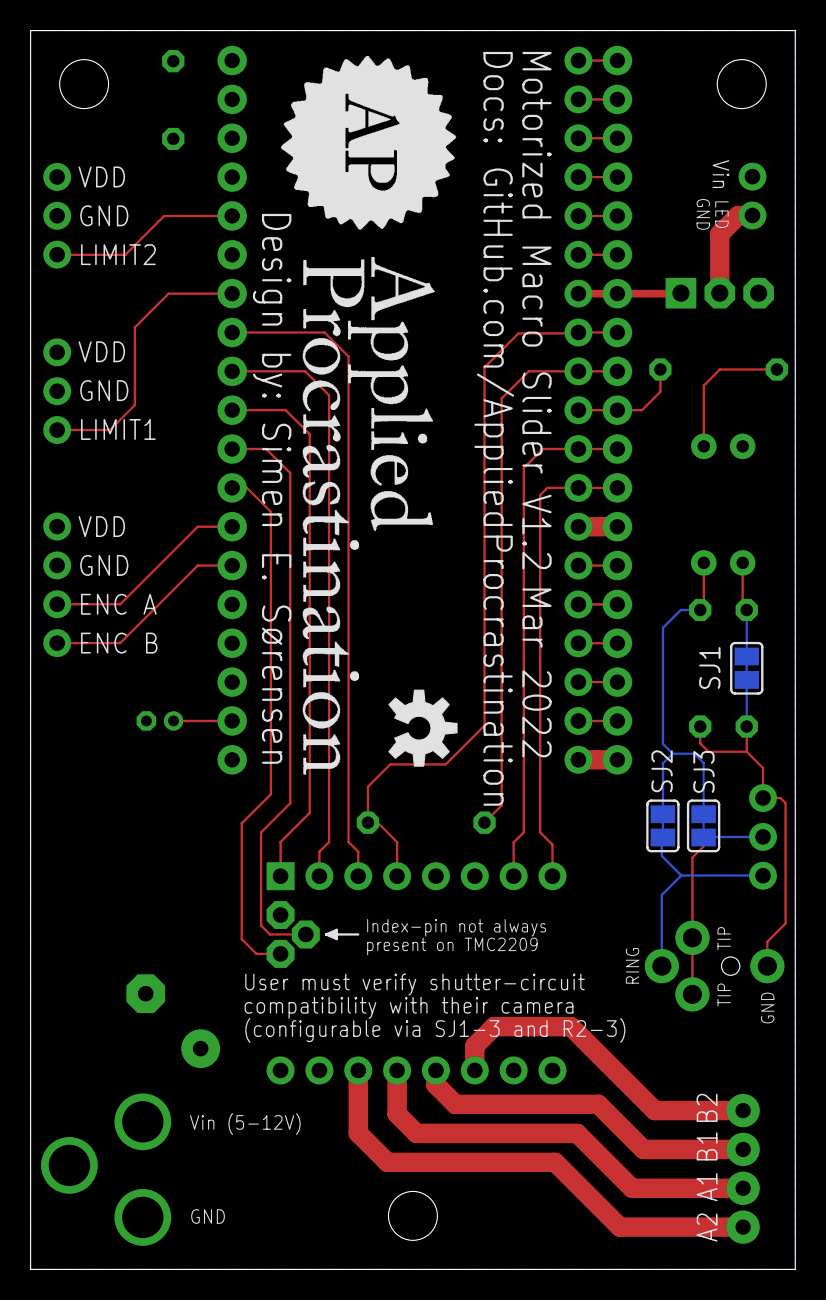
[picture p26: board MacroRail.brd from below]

Board: 2 copper layers, 50.0 x 81.0 mm, 25 parts (5 on the bottom side), 38 nets.

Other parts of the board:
U$2: APPLIED-PROCRASTINATION-FULL
U$3: OSHW-LOGO-M

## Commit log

2022-02-24 Add mounting holes and better outputs
    [MacroRail.brd, MacroRail.sch]
2022-02-24 Adding basic BOM to README
    Adding Bill of Materials and links to example Aliexpress listings.
    [MacroRail.brd, MacroRail.sch]
2022-02-25 Redesigned shutter circuit
    Complete redesign of the shutter circuit to make it more flexible and camera agnostic. The user will have to modify the board to match with what their camera expects.
    [MacroRail.brd, MacroRail.sch]
2022-02-26 V1.0
    Redesigned power planes and added more documentation in silk screen.
    [MacroRail.brd, MacroRail.sch]
2022-02-27 Documentation update
    Initial attempt to describe the camera shutter circuitry.
    [MacroRail.sch]
2022-03-05 Modify BOM and clarify README
2022-03-05 Start V1.1 design
    Add UART Communication between TCM and ESP via SD2 and SD3 pins. Connect DIAG pin. Still undecided whether INDEX pin is necessary as this pin is not always easily accessible on TCM boards.
    [MacroRail.brd, MacroRail.sch]
2022-03-05 Connect DIAG
    [MacroRail.brd]
2022-03-05 V1.1
    Add optional index pin and produce new output files
    [MacroRail.brd, MacroRail.sch]
2022-03-16 Add possibility for driving high power LEDs
    Since good illumination is important for macro photography, an option to drive high power LEDs via the Motorized Macro Rail PCB has been added.
    [MacroRail.brd, MacroRail.sch]
2022-03-22 V1 Revision 1
    Large redesign of the board. Made board wider (50x80mm now). Moved connections to make them more accessible when PCB is mounted on macro slider. Added transistor for driving LED illumination. Added more connections to TMC driver (UART and Index). Added capacitance to EN pin after noticing this helps with automatic bootloader entry during programming.
    [MacroRail.brd, MacroRail.sch]
2022-03-22 Remove outdated gerbers
2022-03-26 Move TMC UART communication to Serial2
    Serial1 is already occupied by the ESP flash, so we need to use Serial2 instead. This interface was already in use by the SHUTTER- and LED_PWM-signals, so they had to be moved as well.
    [MacroRail.brd, MacroRail.sch]
2022-04-03 Update documentation to match V1.2
    V1.2 is the first fully functional design
    [MacroRail.brd]
2022-04-03 Add photos and update README
    Add photographs of V1.1 (with bodge wires making it V1.2 in practice) and update readme
2022-04-23 Add section in readme on how to order the PCB
    Add section in readme on how to order the PCB.
    Add more photos
2022-06-04 Update README.md
    Add links to 3D files at Printables.com and to the FW/Web interface project

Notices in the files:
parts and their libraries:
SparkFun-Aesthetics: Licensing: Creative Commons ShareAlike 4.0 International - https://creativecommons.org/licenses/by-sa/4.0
